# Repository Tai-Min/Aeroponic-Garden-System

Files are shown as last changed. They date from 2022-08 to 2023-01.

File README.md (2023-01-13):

# Thingy:53 Aeroponic Garden
2nd place in [Smarter Sustainable World Challenge
with Nordic Semiconductor](https://www.hackster.io/contests/smarter-sustainable-world). For details of the project itself see [Vertical Self Regulating Soilless Farm](https://www.hackster.io/Tai-Min/vertical-self-regulating-soilless-farm-a86d25)

## Physical setup
### The pot
* Print heater_bottom_n.stl and heater_top_n.stl (n = 1, 2, 3, 4) and glue them together. Insert 12V 5050 fan into place
* Print funnel.stl and insert it into heater glued in previous step
* Print num_layers * 4 layer_quarter.stl and glue them together then stack the layers and place them on top of the heater
* Print num_layers nozzle_frame.stl and num_layers * 4 nozzle_single.stl and glue them together then using straight plastic pipe assemble them starting from funnel's center intlet so that each nozzle_frame is on the level of the pot of given layer  
* Print nozzle_frame_end.stl and insert it at the top of previously created piping
* Print top_hat.stl and insert it at the top of vertical pot then insert Thingy:53 into it 
* Create wooden frame as in the pictures below
* Print valve_holder.stl and screw it at the bottom of the wooden quadropod then screw 12V valves into places
* Print num_layers * 4 - 1 of water_nozzle_frame.stl and nozzle_single.stl and glue them together then screw them on wooden structure so that each nozzle faces one pot
* Print 1 water_nozzle_frame_end.stl and single_nozzle.stl and glue them together and screw it on the wooden structure so it faces one pot
* Install LED strips on wooden structure so each pot has it's own light source

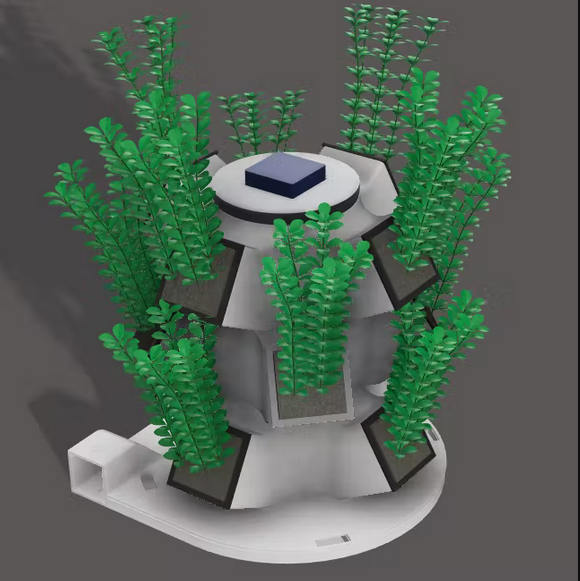
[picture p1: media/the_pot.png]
Pot assembly 1

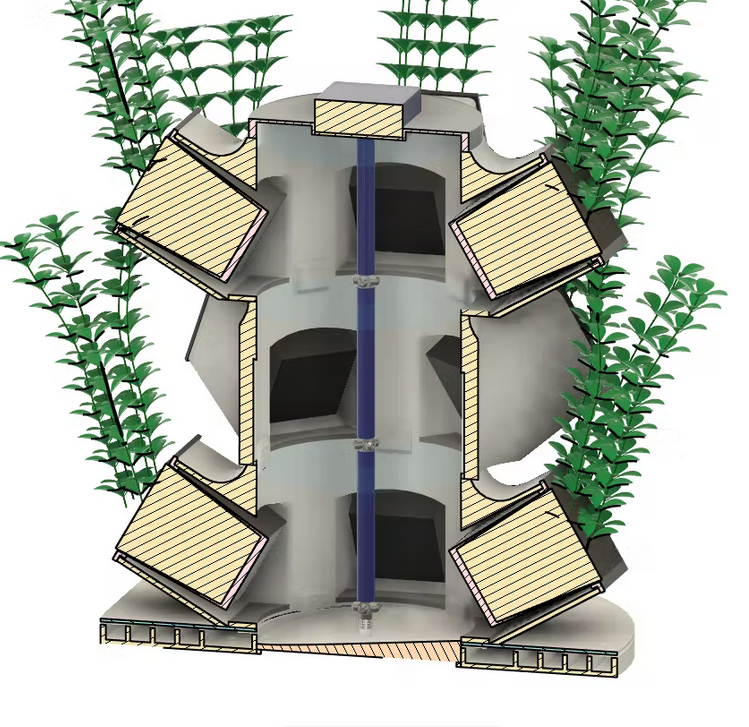
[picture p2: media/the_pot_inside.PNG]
Pot assembly 2

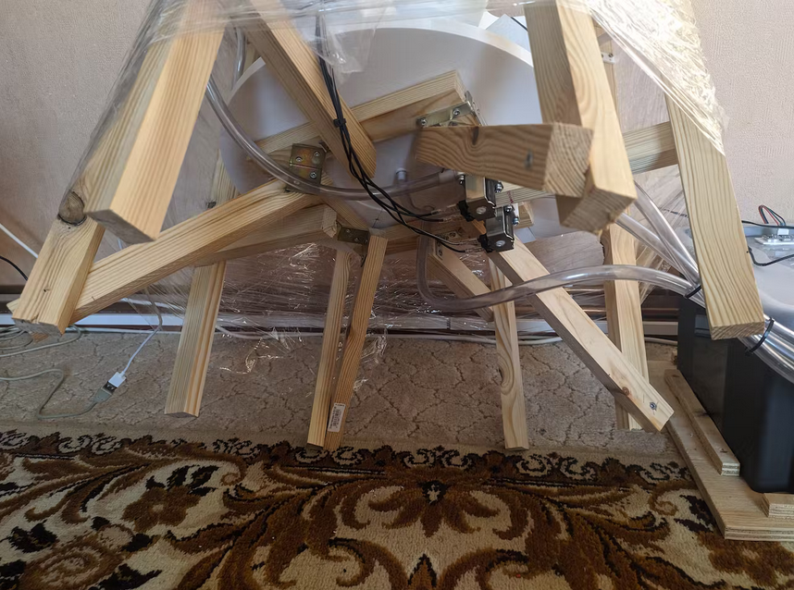
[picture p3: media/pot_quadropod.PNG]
Pot assembly bottom

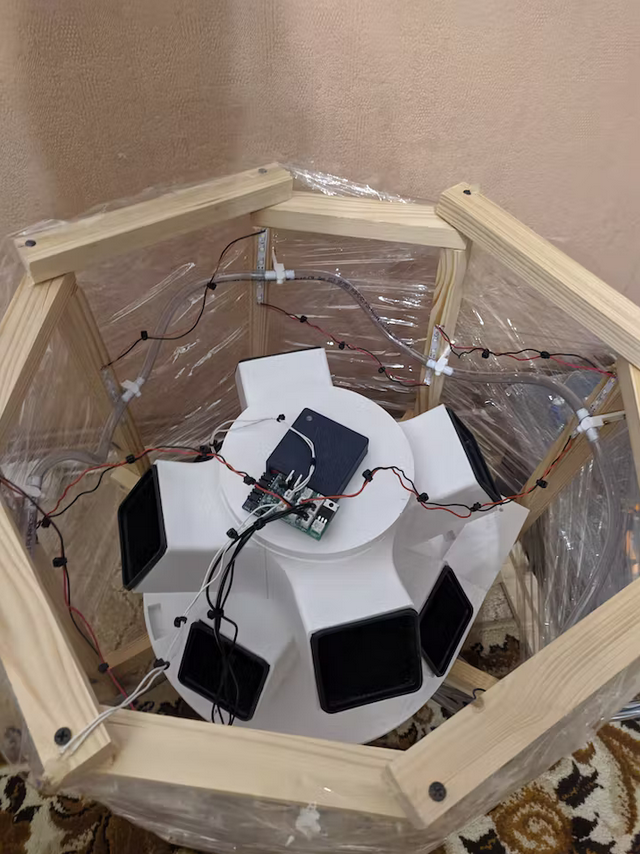
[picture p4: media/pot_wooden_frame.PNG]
Pot assembly frame


### RPi water system
* Print 2 pipe_holder_1.stl and pipe_holder_2.stl and glue them together on the side of both liquid tanks
* Print 2 pump_holder.stl and glue it at the bottom of the tank then screw the 12V pump into it
* Print 2 water_level_holder.stl, place it on the lids of both liquid tanks and then snap an ultrasonic sensor into them
* Screw reed switches into both liquid tanks and corresponding magnets into lids
* On nutrition water tank mount PCBs for EC and pH sensors and place the sensors into the tank itself
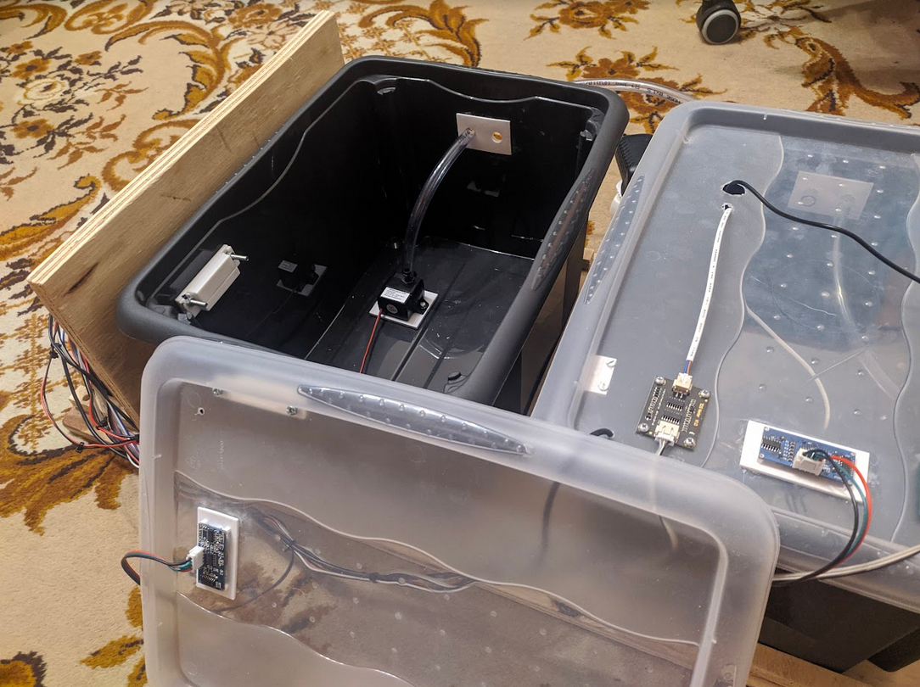
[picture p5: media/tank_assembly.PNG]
Tank assembly


### Putting it together
Use flexible piping to connect the pot to water system as in the block diagram below:
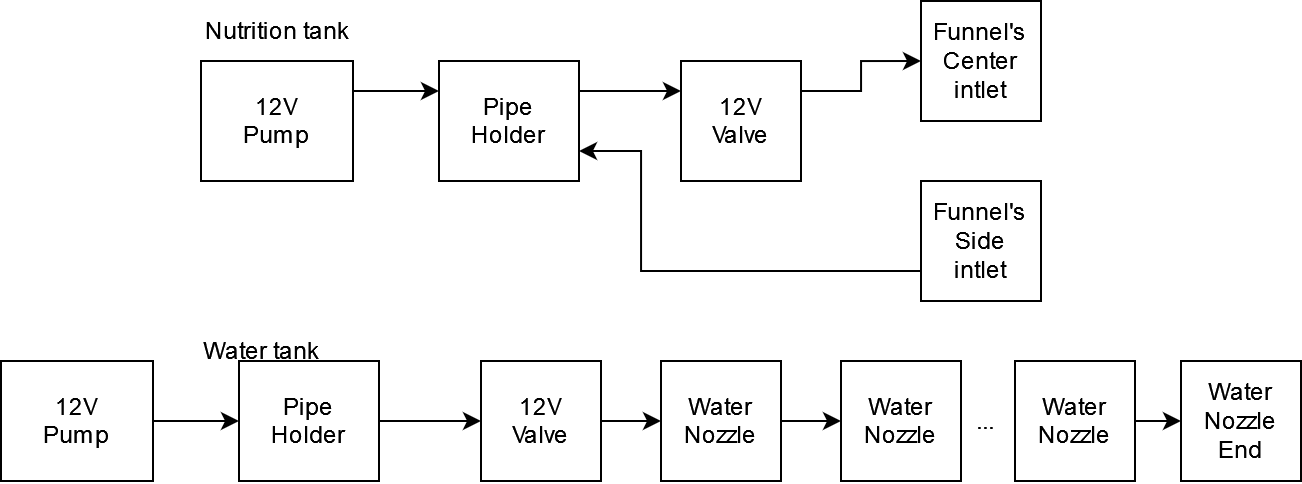
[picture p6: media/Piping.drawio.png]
Piping diagram


## Electronics
Refer to KiCad project in /pi_shield folder for BOM and assembly purposes of the hats.

### The pot
Connect sensors / actuators to Thingy:53 control hat as in the block diagram below:
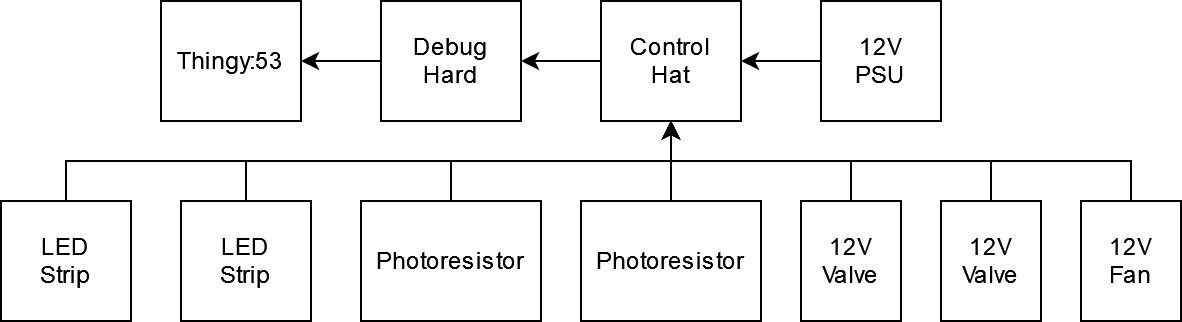
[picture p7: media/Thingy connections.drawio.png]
Thingy:53 connections


### RPi water system
Connect sensors / actuators to RPi's control hat as in the block diagram below:
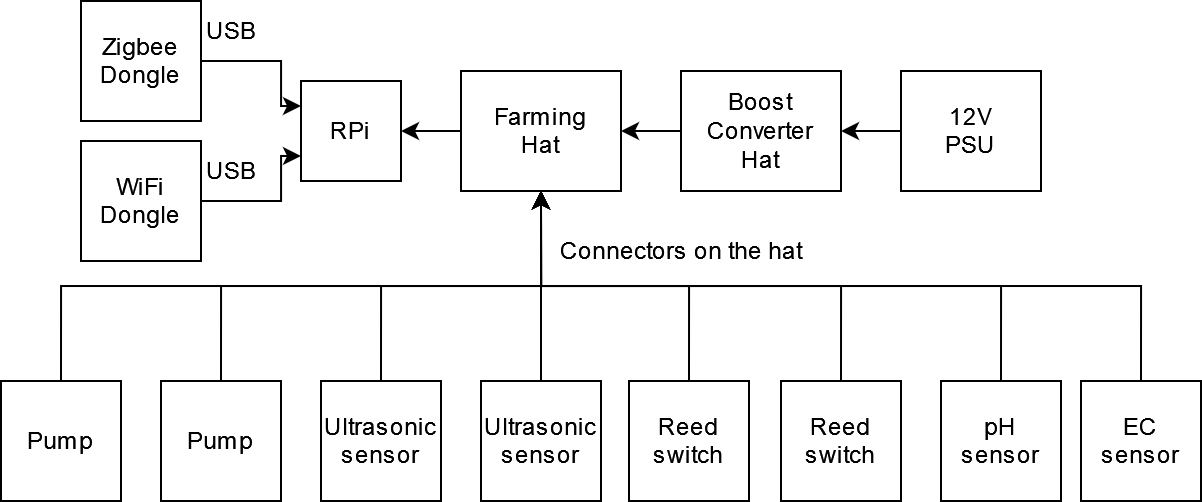
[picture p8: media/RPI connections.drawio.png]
RPi connections

## Attiny85
* Connect some programmer (i.e. ArduinoISP or USBasp) to Attiny85
* In platformio.ini change upload_protocol to your programmer
* You might also want to fine tune PH_MAGIC_NUMBER, TDS_A, TDS_B variables to match your sensor's characteristics
* In PlatformIO menu press "Set Fuses" in "attiny85" configuration, then click "Upload"
* Insert Attiny85 into Farm Overseers's shield

## Farm Overseer setup
* Setup Ubuntu Server 20.04 (i.e via [Raspberry Pi Imager](https://www.raspberrypi.com/software/))

### Enable UART
* Disable serial console
```
sudo systemctl stop serial-getty@ttyS0.service
sudo systemctl disable serial-getty@ttyS0.service
sudo systemctl mask serial-getty@ttyS0.service
```
* Put below into /etc/udev/rules.d/10-local.rules
```
KERNEL=="ttyS0", SYMLINK+="serial0" GROUP="tty" MODE="0660"
KERNEL=="ttyAMA0", SYMLINK+="serial1" GROUP="tty" MODE="0660"
```
* Reload udev rules
```
sudo udevadm control --reload-rules && sudo udevadm trigger
```
* Add user to tty (edit parts in "<>")
```
sudo adduser <USER> tty
```
* Delete below from /boot/firmware/cmdline.txt
```
console=serial0,115200
```
* Add below to /boot/firmware/config.txt
```
dtoverlay=disable-bt
```
### Enable 1-Wire
* Add below to /boot/firmware/config.txt
```
dtoverlay=w1-gpio,gpiopin=4
```

### ROS2
* Install [ROS2 Foxy Base version](https://docs.ros.org/en/foxy/Installation/Ubuntu-Install-Debians.html)
* Clone this repo to your home directory (/home/$USER/TODO)
* Build ROS components:
```bash
cd ~/TODO/ros_workspace && colcon build
```
* Place ROS setups in your .bashrc (edit parts in "<>")
```
source /opt/ros/foxy/setup.bash
source /home/<USER>/TODO/ros_workspace/install/setup.bash

```
### Mosquitto
* Install mosquitto 2.0
```
sudo add-apt-repository -y ppa:mosquitto-dev/mosquitto-ppa
sudo apt install mosquitto
sudo systemctl enable mosquitto
```

### zigbee2mqtt
* Install [zigbee2mqtt](https://www.zigbee2mqtt.io/guide/installation/01_linux.html) and set it to start as a daemon on boot. Use following config (edit parts in "<>"):
```yaml
mqtt:
  base_topic: field
  server: 'mqtt://localhost'

serial:
  port: <YOUR ZIGBEE DONGLE PORT>

advanced:
    network_key: GENERATE

external_converters:
  - fc.js
```

Create file /opt/zigbee2mqtt/data/fc.js and paste following into it:
```js
const fz = require('zigbee-herdsman-converters/converters/fromZigbee');
const tz = require('zigbee-herdsman-converters/converters/toZigbee');
const exposes = require('zigbee-herdsman-converters/lib/exposes');
const reporting = require('zigbee-herdsman-converters/lib/reporting');

const definition = {
    zigbeeModel: ['FC_v0.1'],
    model: 'FC',
    vendor: 'Nordic',
    description: 'Field Controller',
    fromZigbee: [fz.temperature, fz.humidity, fz.pressure, fz.on_off, fz.level_config],
    toZigbee: [tz.on_off, tz.level_config],
    exposes: [],
    configure: async (device, coordinatorEndpoint, logger) => {
        await reporting.bind(device.getEndpoint(16), coordinatorEndpoint, ['msTemperatureMeasurement']);
        await reporting.temperature(device.getEndpoint(16), { min: 30, max: 30, change: 0 });

        await reporting.bind(device.getEndpoint(16), coordinatorEndpoint, ['msPressureMeasurement']);
        await reporting.pressure(device.getEndpoint(16), { min: 30, max: 30, change: 0 });

        await reporting.bind(device.getEndpoint(16), coordinatorEndpoint, ['msRelativeHumidity']);
        await reporting.humidity(device.getEndpoint(16), { min: 30, max: 30, change: 0 });
    },
    endpoint: (device) => {
        return { fan: 10, led1: 11, led2: 12, strat: 13, water_valve: 14, nutri_valve: 15, sensors: 16 };
    },
};

module.exports = definition;
```

### Finishing up
* Reboot the board
```
sudo reboot now
```

## Field controller setup
Open field_controller/ in VSCode with nRF Connect and with Thingy:53 connected via JLink press flash.

## Run Farm Overseer's control algorithms
SSH into the Farm Overseer and run:
```
ros2 launch garden_meta system.launch.py
```

## Pair field controller to Farm Overseer
With Field Controller running cd into scripts/ and run:
```
./pair.sh -t 300
``` 
This will enable pairing for 300 seconds and should pair with the Field Controller.

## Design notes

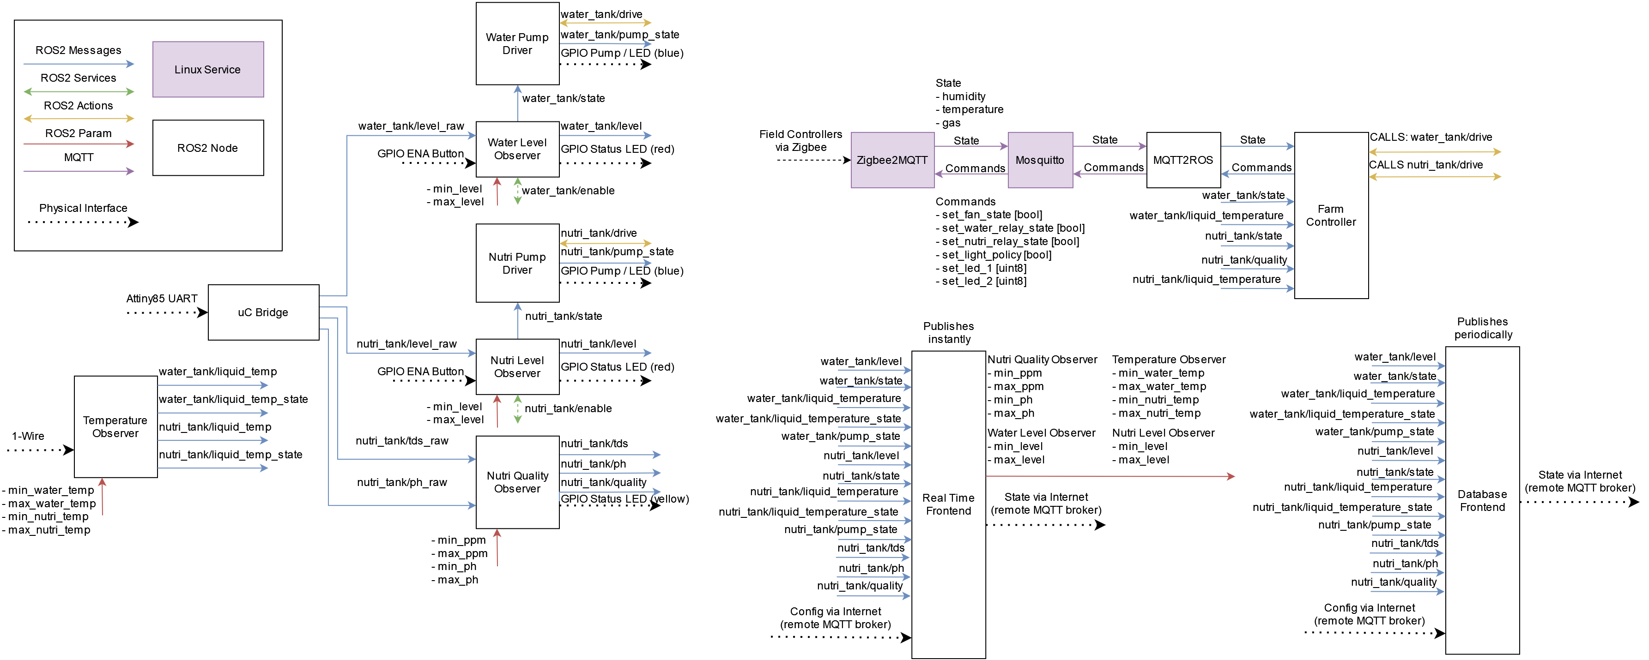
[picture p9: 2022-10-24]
media/controller_software.drawio.png

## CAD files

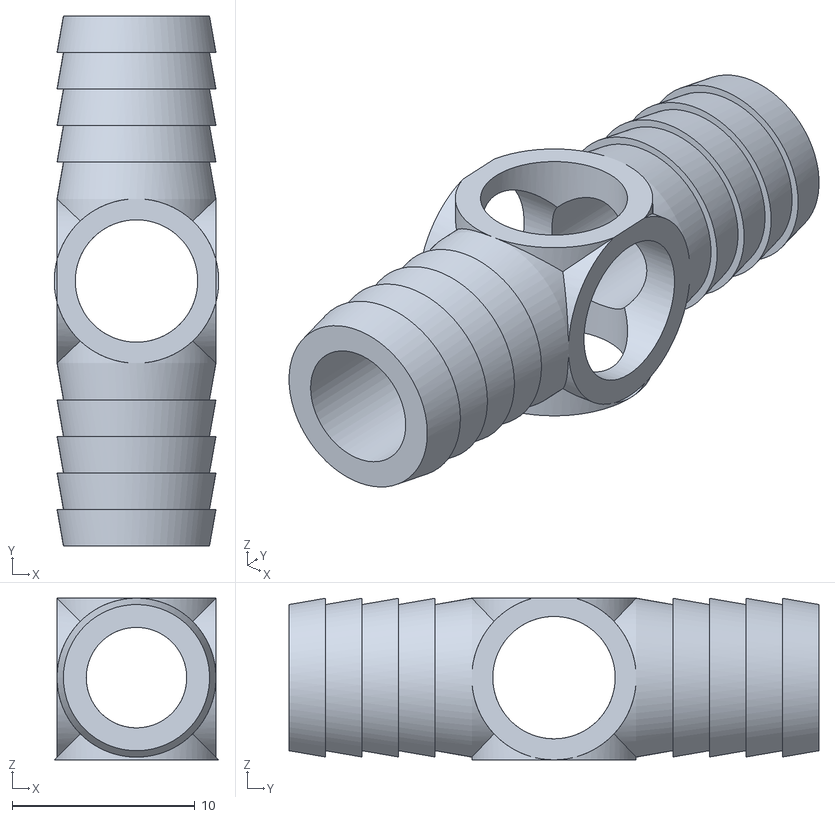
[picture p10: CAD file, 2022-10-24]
stl/nozzle_frame.stl
9.00 x 29.0 x 8.85

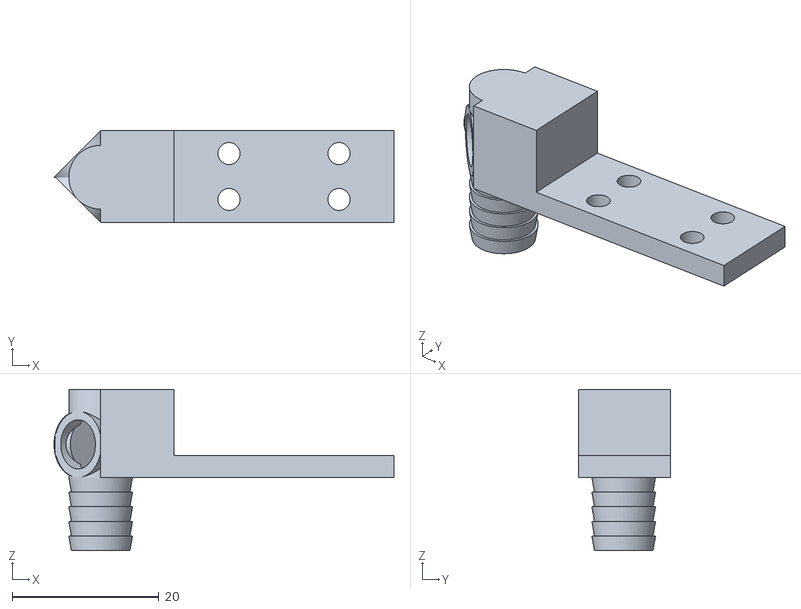
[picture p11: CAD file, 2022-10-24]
stl/water_nozzle_frame_end.stl
46.4 x 12.5 x 22.0

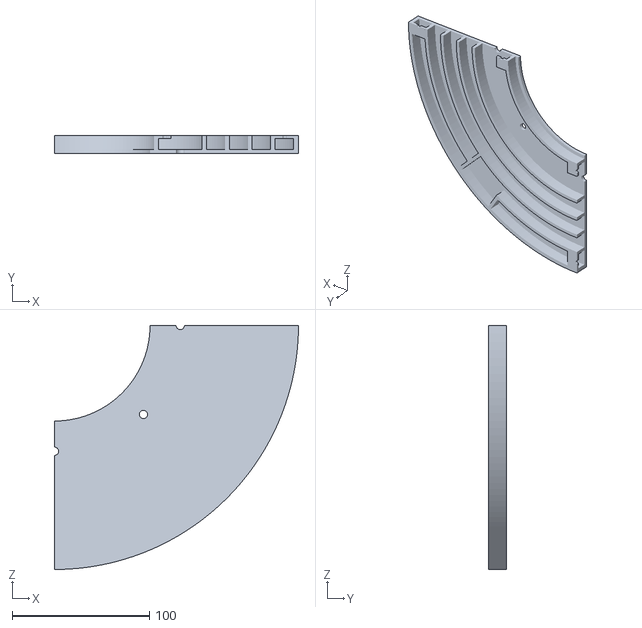
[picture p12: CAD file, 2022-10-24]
stl/heater_bottom_2.stl
177.5 x 13.0 x 177.5

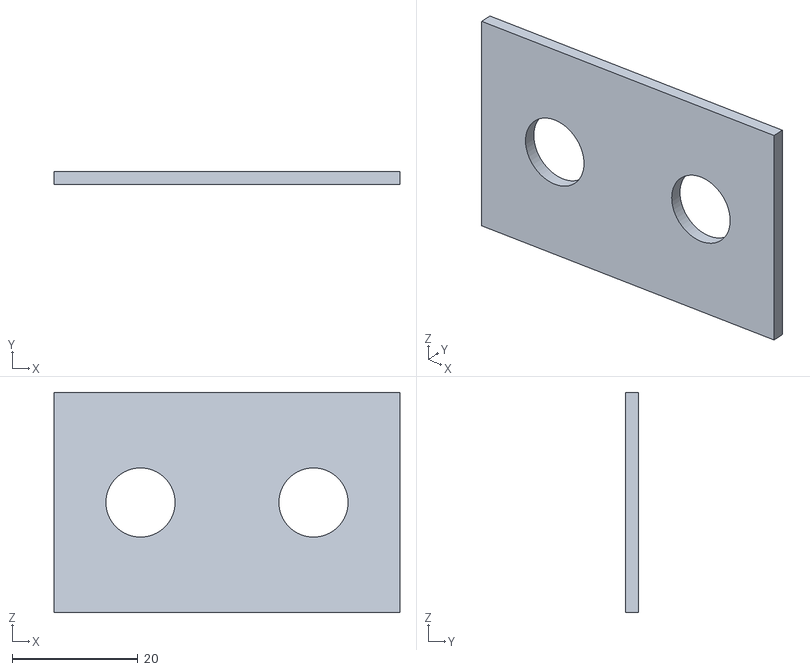
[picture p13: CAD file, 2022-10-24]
stl/pipe_holder_1.stl
55.0 x 2.00 x 35.0

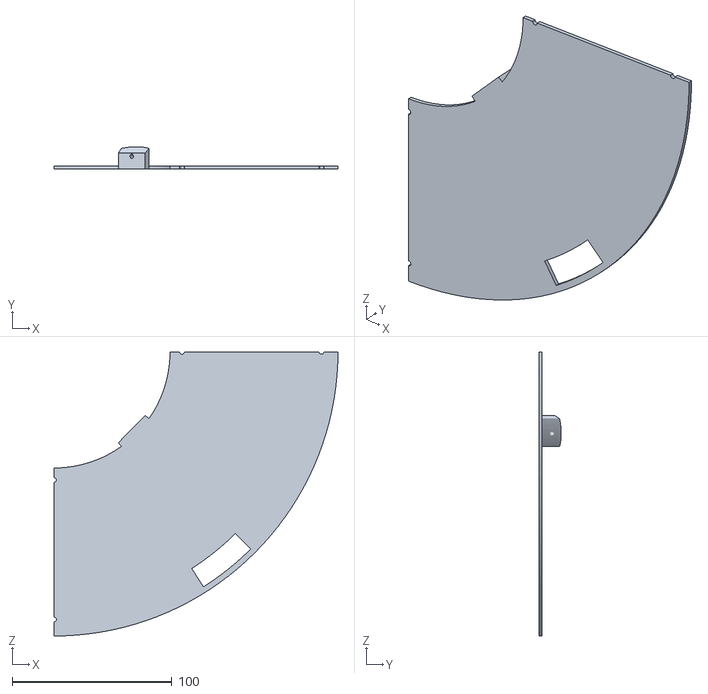
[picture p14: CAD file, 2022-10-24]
stl/heater_top_3.stl
177.5 x 14.0 x 177.5

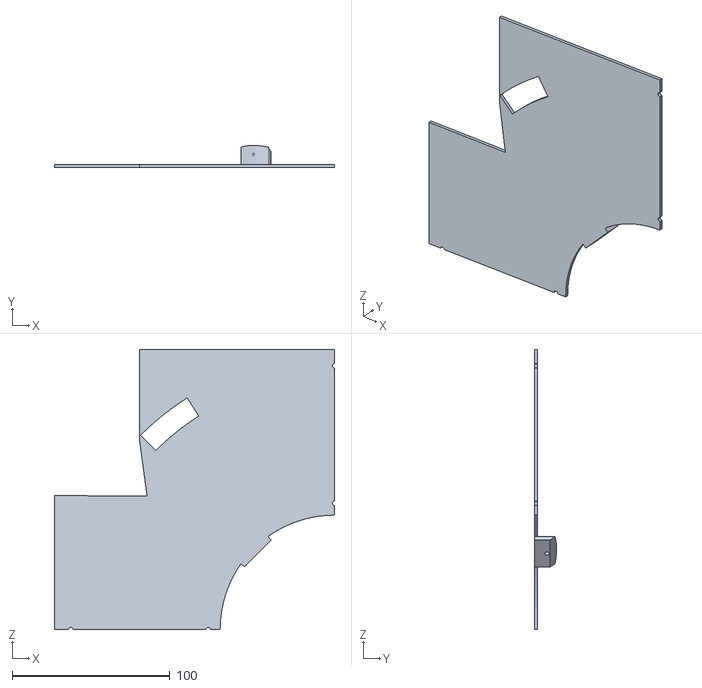
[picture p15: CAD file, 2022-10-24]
stl/heater_top_1.stl
177.4 x 14.0 x 177.5

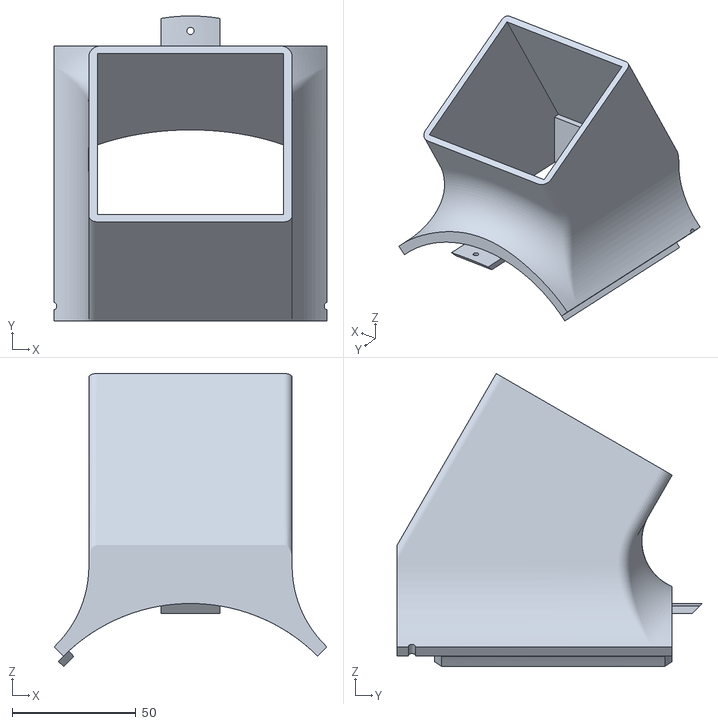
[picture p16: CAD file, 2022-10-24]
stl/layer quarter.stl
110.0 x 123.0 x 118.2

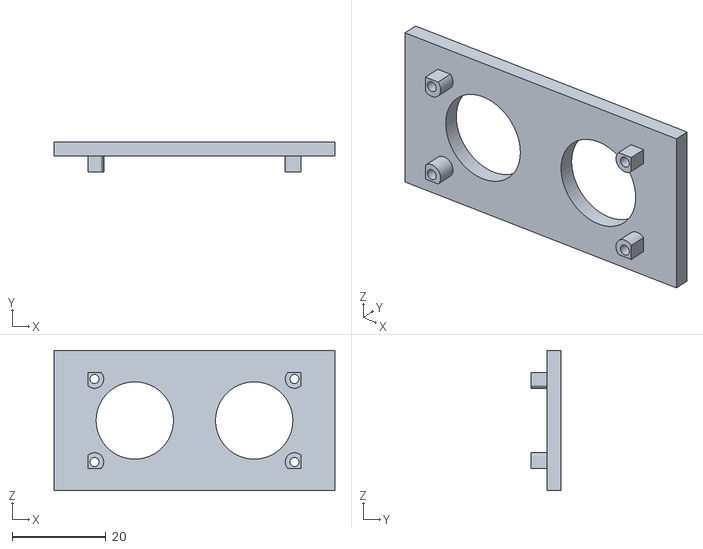
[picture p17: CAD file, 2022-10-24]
stl/water_level_holder.stl
60.0 x 6.50 x 30.0

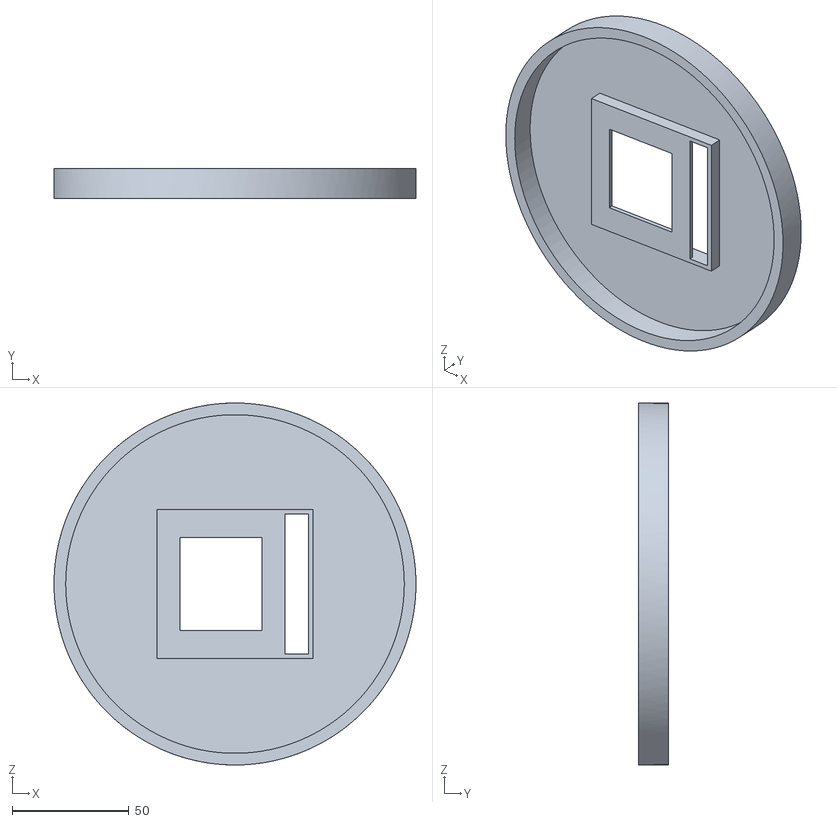
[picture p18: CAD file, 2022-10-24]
stl/top_hat.stl
155.0 x 13.0 x 155.0

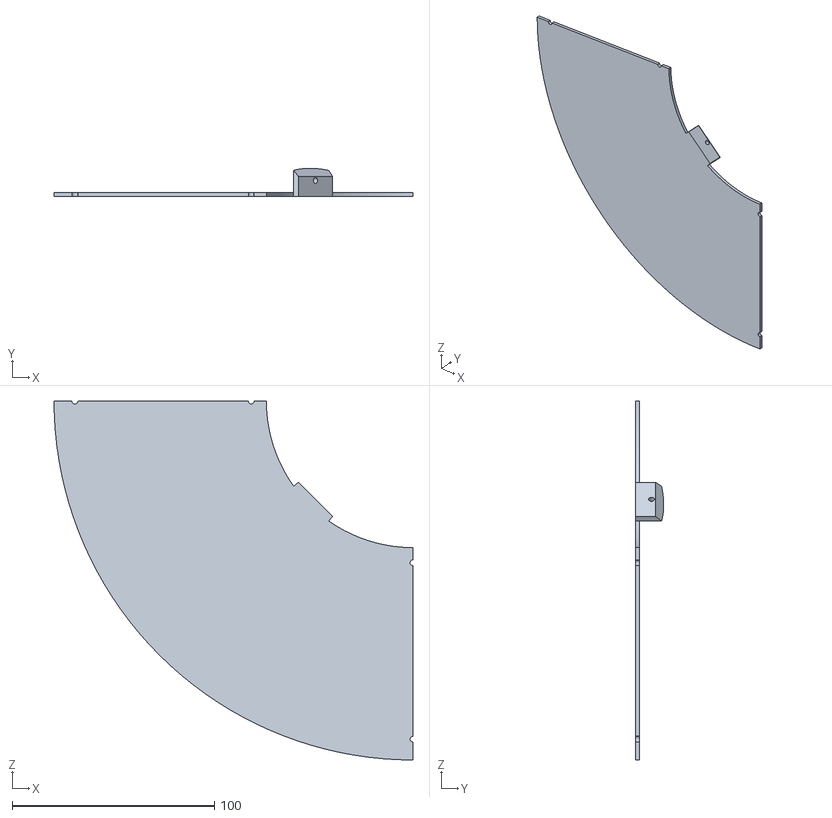
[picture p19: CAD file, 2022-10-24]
stl/heater_top_2.stl
177.5 x 14.0 x 177.5

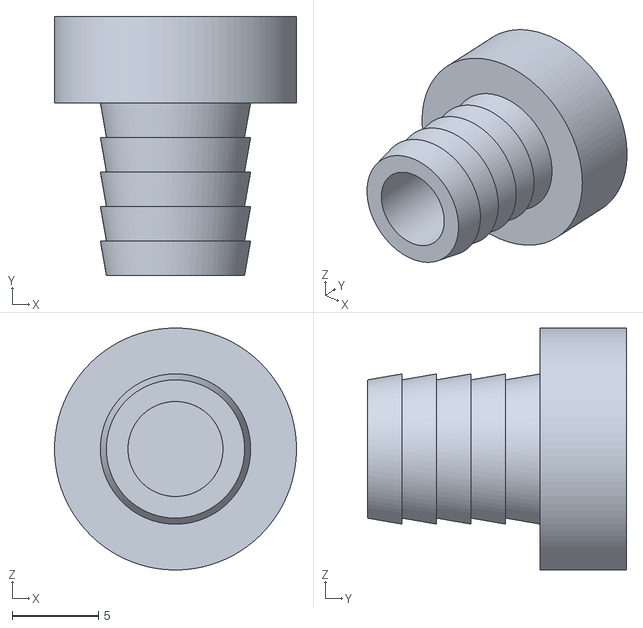
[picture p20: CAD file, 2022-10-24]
stl/nozzle_frame_end.stl
14.0 x 15.0 x 14.0

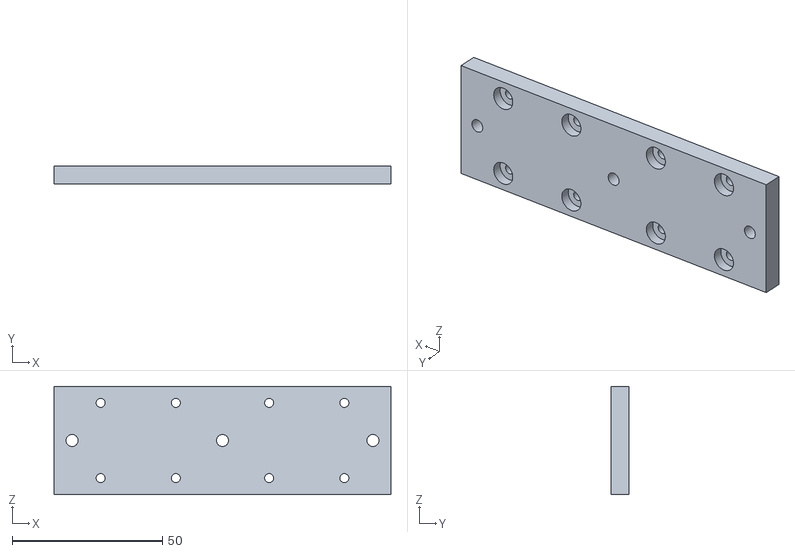
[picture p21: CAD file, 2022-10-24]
stl/valve_holder.stl
112.0 x 6.00 x 36.0

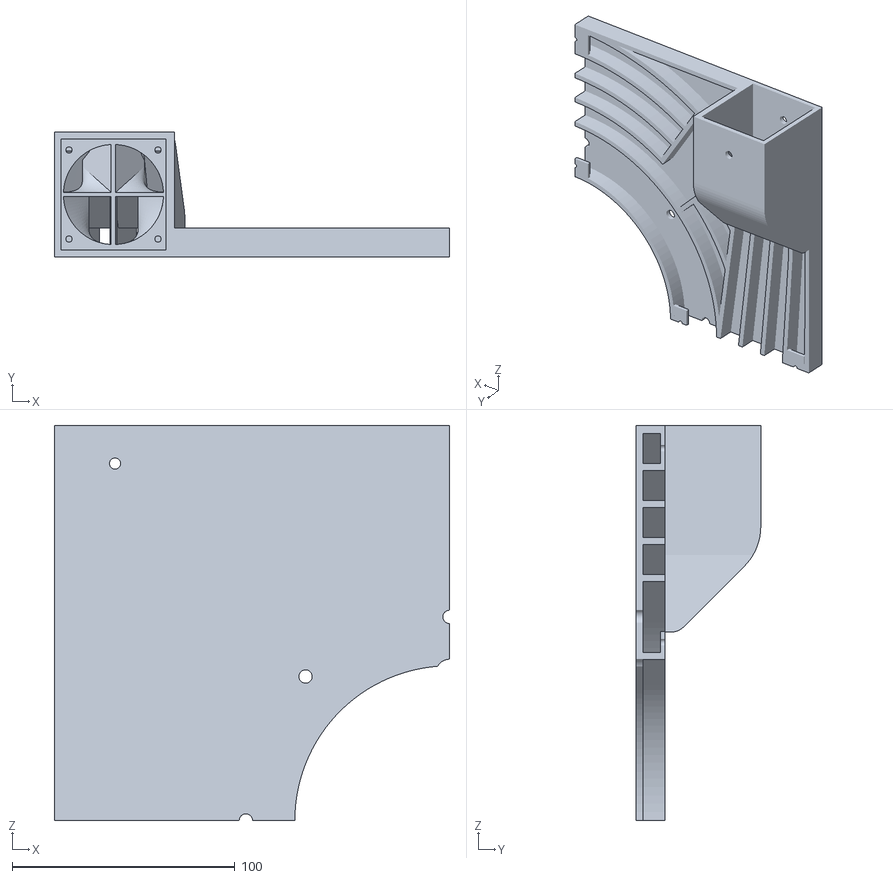
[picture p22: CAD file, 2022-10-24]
stl/heater_bottom_4.stl
177.5 x 56.0 x 177.5

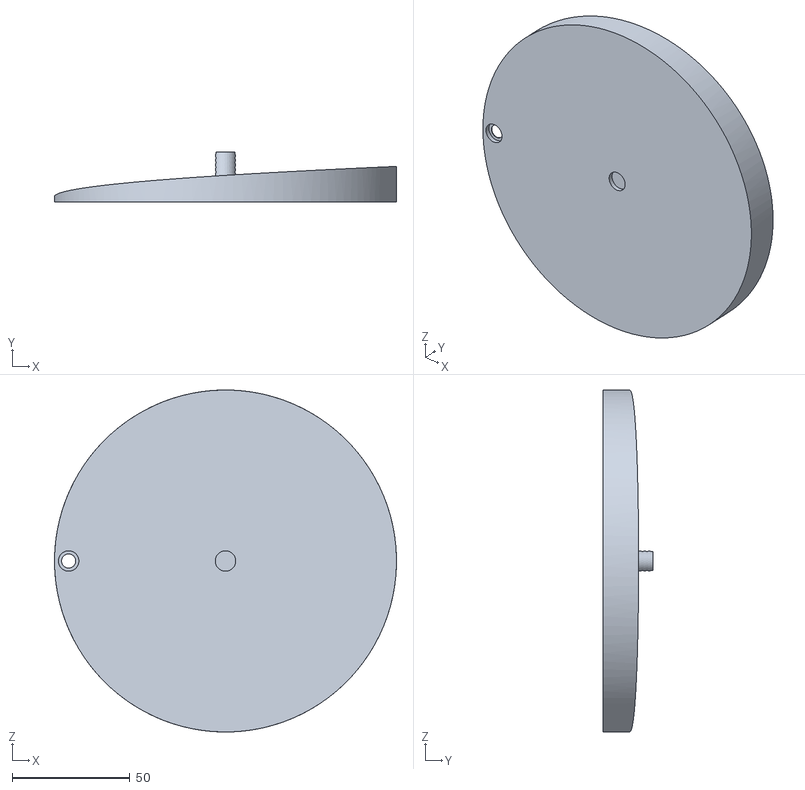
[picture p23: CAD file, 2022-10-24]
stl/funnel.stl
145.0 x 21.0 x 145.0

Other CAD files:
stl/heater_top_4.stl
stl/heater_bottom_1.stl
stl/nozzle_single.stl
stl/pipe_holder_2.stl
stl/heater_bottom_3.stl
stl/pump_holder.stl
stl/water_nozzle_frame.stl

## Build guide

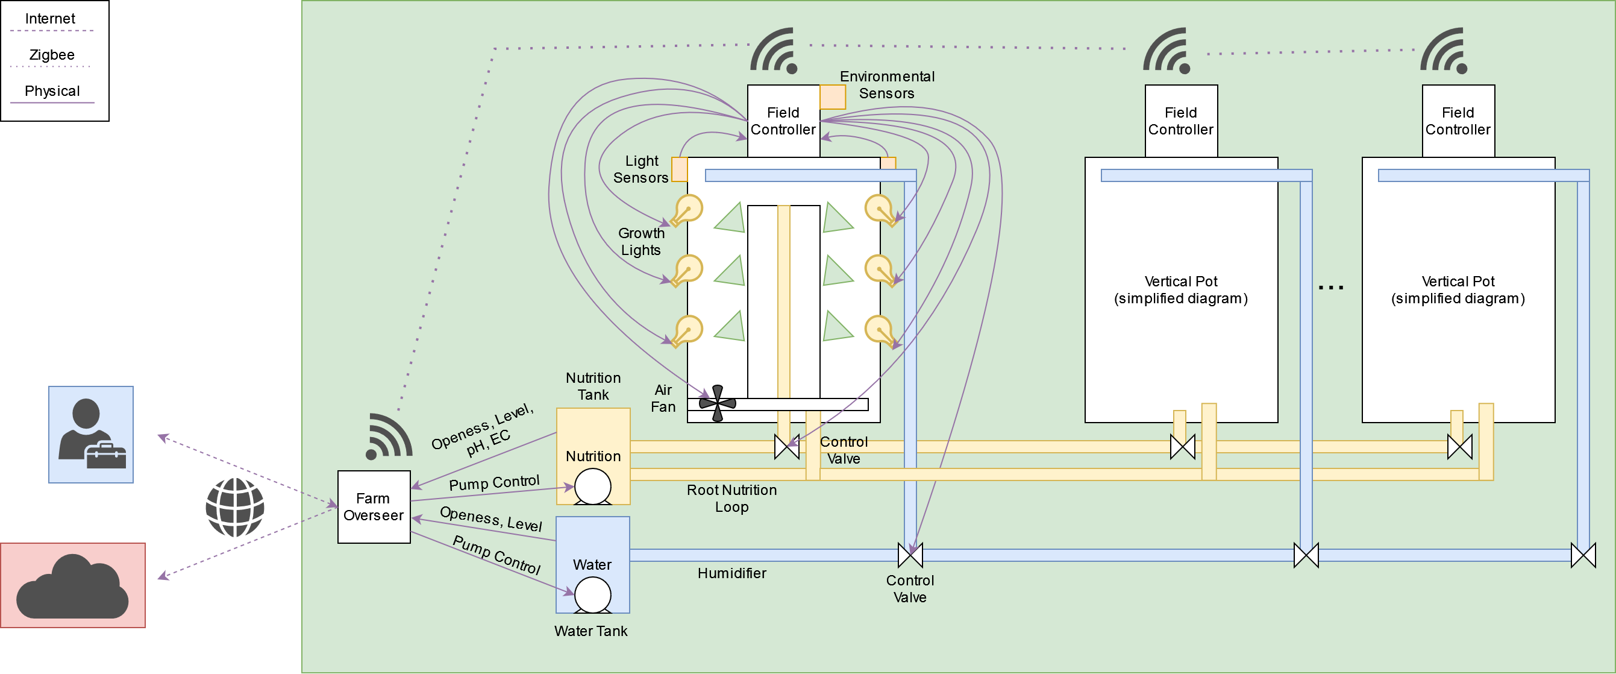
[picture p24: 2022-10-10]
media/system_setup_detailed.drawio.png

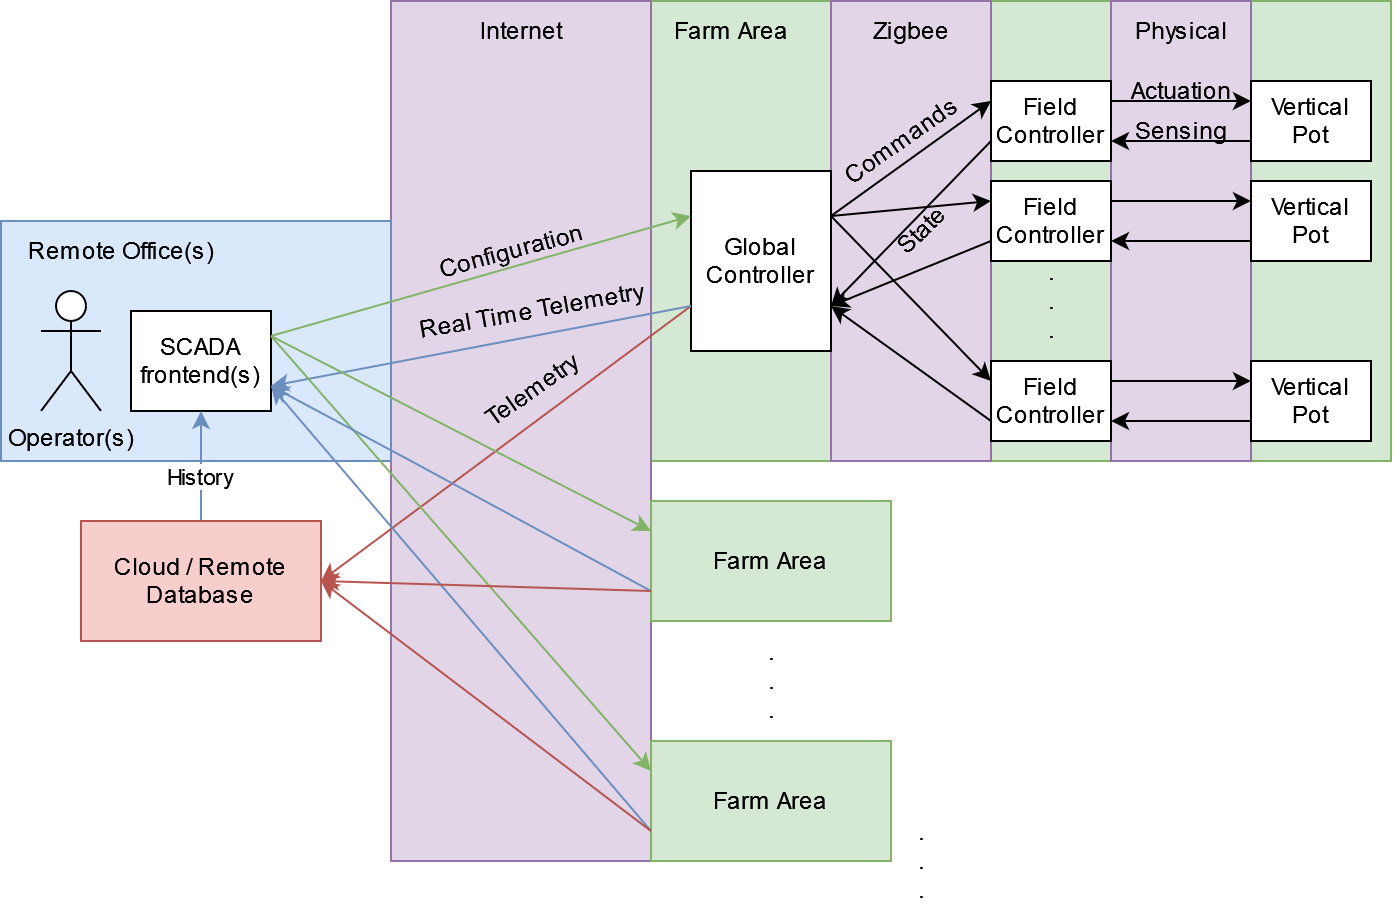
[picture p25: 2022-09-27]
media/system_setup.drawio.png

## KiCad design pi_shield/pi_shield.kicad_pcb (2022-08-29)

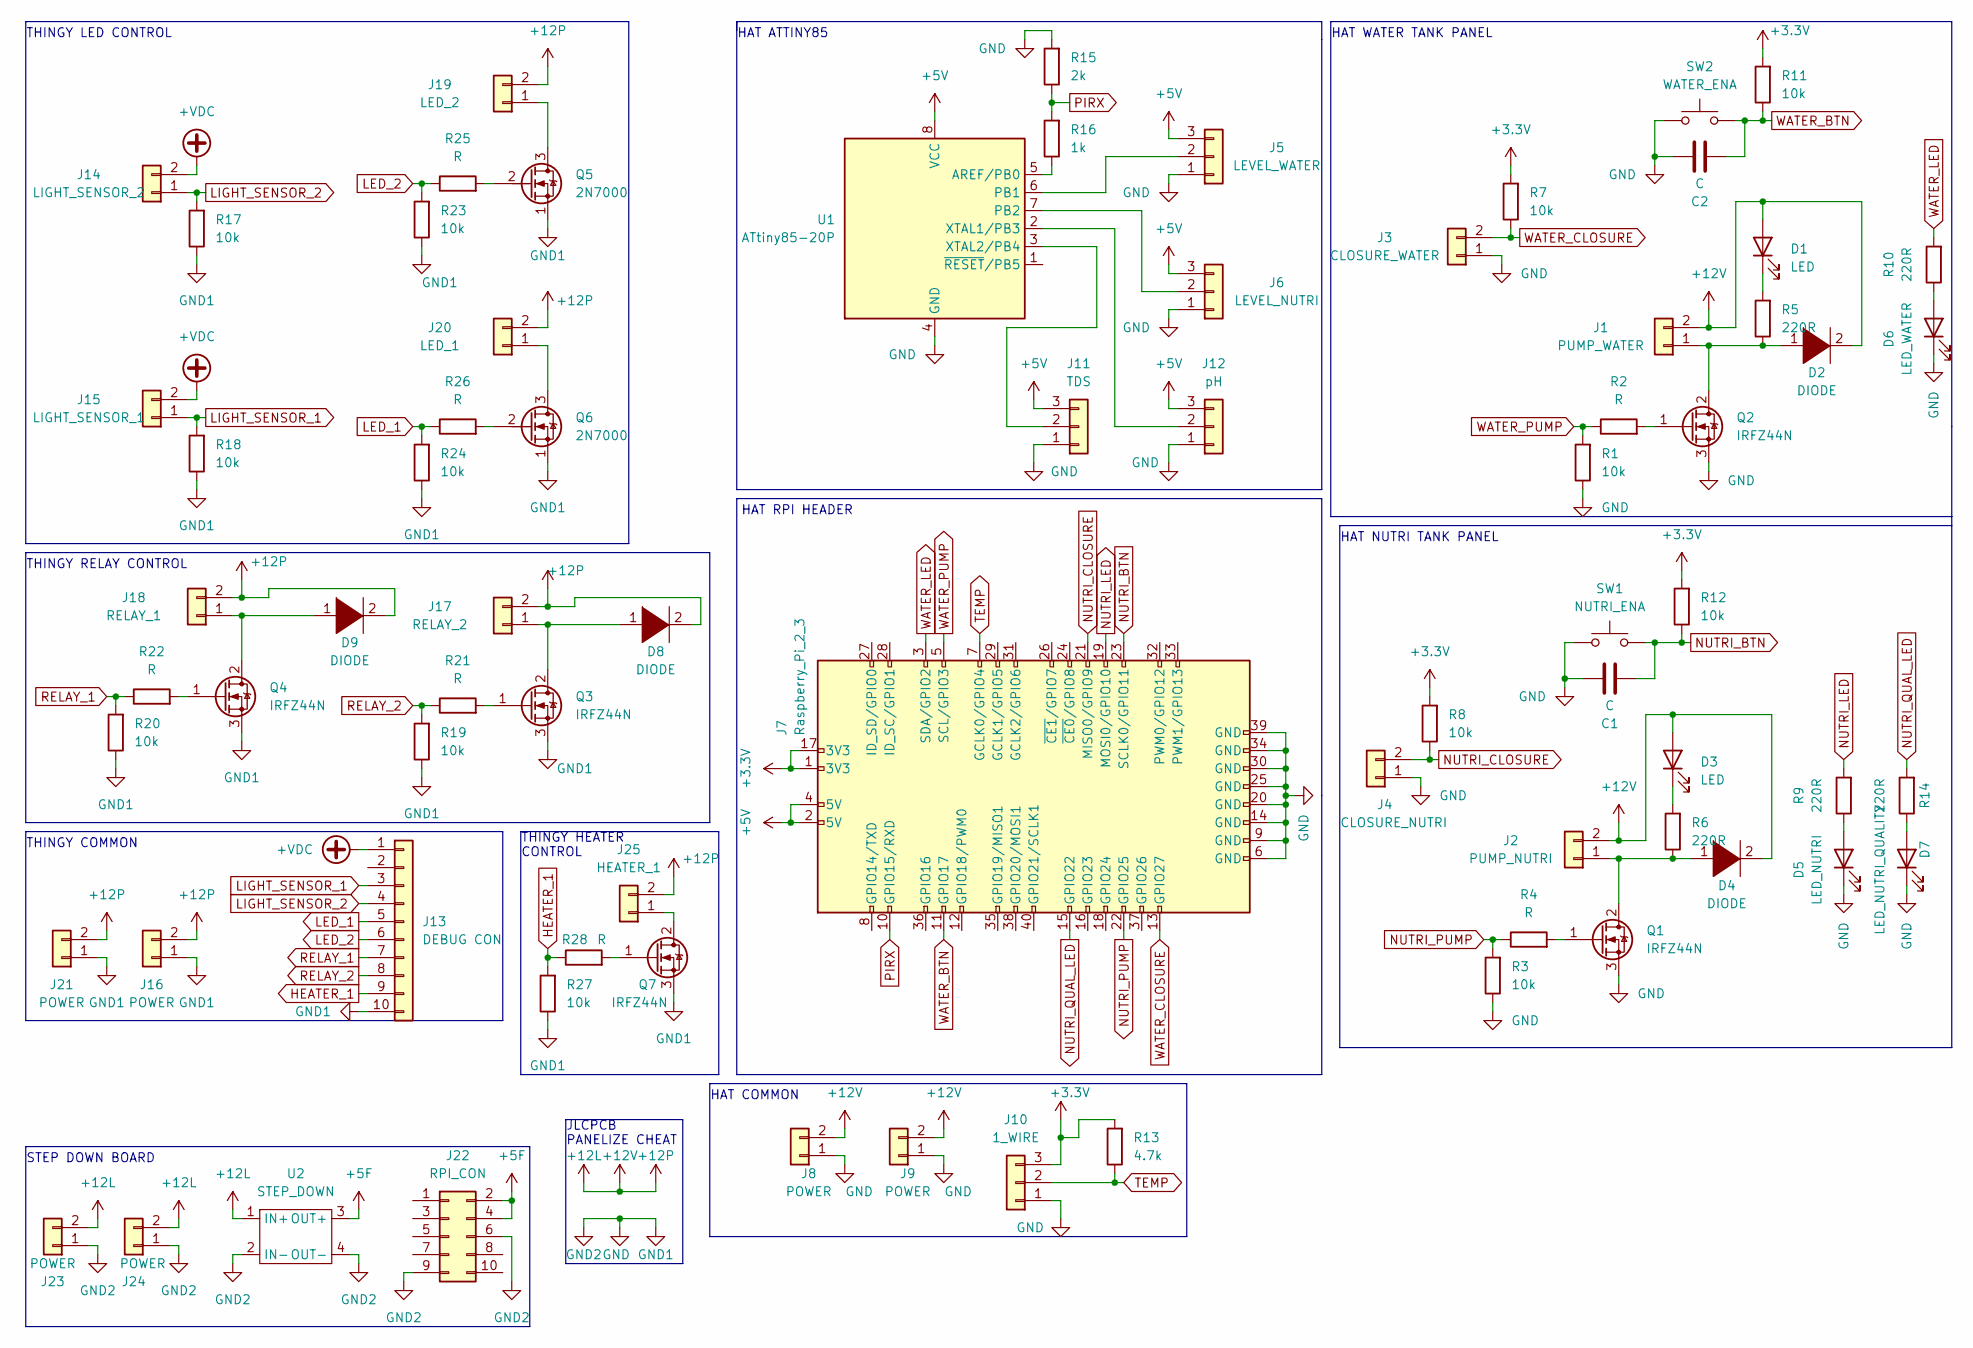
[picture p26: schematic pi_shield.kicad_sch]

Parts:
C1, C2: C; C_Disc_D5.0mm_W2.5mm_P2.50mm
D1, D3: LED; LED_D5.0mm_Clear
D2: DIODE; D_DO-15_P2.54mm_Vertical_AnodeUp
D4, D8, D9: DIODE; D_A-405_P2.54mm_Vertical_AnodeUp
D5: LED_NUTRI; LED_D5.0mm_Clear
D6: LED_WATER; LED_D5.0mm_Clear
D7: LED_NUTRI_QUALITY; LED_D5.0mm_Clear
J1: PUMP_WATER; Molex_SL_171971-0002_1x02_P2.54mm_Vertical
J2: PUMP_NUTRI; Molex_SL_171971-0002_1x02_P2.54mm_Vertical
J3: CLOSURE_WATER; Molex_SL_171971-0002_1x02_P2.54mm_Vertical
J4: CLOSURE_NUTRI; Molex_SL_171971-0002_1x02_P2.54mm_Vertical
J5: LEVEL_WATER; Molex_SL_171971-0003_1x03_P2.54mm_Vertical
J6: LEVEL_NUTRI; Molex_SL_171971-0003_1x03_P2.54mm_Vertical
J7: Raspberry_Pi_2_3; raspberrypi_2_3
J8, J9, J16, J21, J23, J24: POWER; Molex_SL_171971-0002_1x02_P2.54mm_Vertical
J10: 1_WIRE; Molex_SL_171971-0003_1x03_P2.54mm_Vertical
J11: TDS; Molex_SL_171971-0003_1x03_P2.54mm_Vertical
J12: pH; Molex_SL_171971-0003_1x03_P2.54mm_Vertical
J13: DEBUG CON; PinSocket_1x10_P2.54mm_Vertical
J14: LIGHT_SENSOR_2; Molex_SL_171971-0002_1x02_P2.54mm_Vertical
J15: LIGHT_SENSOR_1; Molex_SL_171971-0002_1x02_P2.54mm_Vertical
J17: RELAY_2; Molex_SL_171971-0002_1x02_P2.54mm_Vertical
J18: RELAY_1; Molex_SL_171971-0002_1x02_P2.54mm_Vertical
J19: LED_2; Molex_SL_171971-0002_1x02_P2.54mm_Vertical
J20: LED_1; Molex_SL_171971-0002_1x02_P2.54mm_Vertical
J22: RPI_CON; PinSocket_2x05_P2.54mm_Vertical
J25: HEATER_1; Molex_SL_171971-0002_1x02_P2.54mm_Vertical
Q1, Q2, Q7: IRFZ44N; TO-220-3_Horizontal_TabDown
Q3, Q4: IRFZ44N; TO-220-3_Vertical
Q5, Q6: 2N7000; TO-92L_Inline
R1, R3, R7, R8, R11, R12, R17, R18, R19, R20, R23, R24, R27: 10k; R_Axial_DIN0204_L3.6mm_D1.6mm_P2.54mm_Vertical
R2, R4, R21, R22, R25, R26, R28: R; R_Axial_DIN0204_L3.6mm_D1.6mm_P2.54mm_Vertical
R5, R6, R9, R10, R14: 220R; R_Axial_DIN0204_L3.6mm_D1.6mm_P2.54mm_Vertical
R13: 4.7k; R_Axial_DIN0204_L3.6mm_D1.6mm_P2.54mm_Vertical
R15: 2k; R_Axial_DIN0204_L3.6mm_D1.6mm_P2.54mm_Vertical
R16: 1k; R_Axial_DIN0204_L3.6mm_D1.6mm_P2.54mm_Vertical
SW1: NUTRI_ENA; SW_PUSH_6mm
SW2: WATER_ENA; SW_PUSH_6mm
U1: ATtiny85-20P; DIP-8_W7.62mm
U2: STEP_DOWN; SRT_MPT1584EN_Module

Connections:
+3.3V: J7.1 (3V3), J7.17 (3V3), J10.3, R7.2, R8.2, R11.2, R12.2, R13.2
+5F: J22.2, J22.4, U2.3 (OUT+)
+5V: J5.3, J6.3, J7.2 (5V), J7.4 (5V), J11.3, J12.3, U1.8 (VCC)
+12L: D1.2 (A), D2.2 (A), D3.2 (A), D4.2 (A), D8.2 (A), D9.2 (A), J1.2, J2.2, J8.2, J9.2, J16.2, J17.2, J18.2, J19.2, J20.2, J21.2, J23.2, J24.2, J25.2, U2.1 (IN+)
+VDC: J13.1, J14.2, J15.2
GND: C1.1, C2.1, D5.1 (K), D6.1 (K), D7.1 (K), J3.1, J4.1, J5.1, J6.1, J7.6 (GND), J7.9 (GND), J7.14 (GND), J7.20 (GND), J7.25 (GND), J7.30 (GND), J7.34 (GND), J7.39 (GND), J8.1, J9.1, J10.1, J11.1, J12.1, J13.10, J16.1, J21.1, J22.6, J22.9, J23.1, J24.1, Q1.3 (S), Q2.3 (S), Q3.3 (S), Q4.3 (S), Q5.1 (S), Q6.1 (S), Q7.3 (S), R1.1, R3.1, R15.2, R17.1, R18.1, R19.1, R20.1, R23.1, R24.1, R27.1, SW1.1, SW2.1, U1.4 (GND), U2.2 (IN-), U2.4 (OUT-)
HEATER_1: J13.9, R27.2, R28.1
LED_1: J13.5, R24.2, R26.1
LED_2: J13.6, R23.2, R25.1
LIGHT_SENSOR_1: J13.3, J15.1, R18.2
LIGHT_SENSOR_2: J13.4, J14.1, R17.2
NUTRI_BTN: C1.2, J7.23 (SCLK0/GPIO11), R12.1, SW1.2
NUTRI_CLOSURE: J4.2, J7.21 (MISO0/GPIO9), R8.1
NUTRI_LED: J7.19 (MOSI0/GPIO10), R9.2
NUTRI_PUMP: J7.22 (GPIO25), R3.2, R4.1
NUTRI_QUAL_LED: J7.15 (GPIO22), R14.2
unnamed: D1.1 (K), R5.2
unnamed: D2.1 (K), J1.1, Q2.2 (D), R5.1
unnamed: D3.1 (K), R6.2
unnamed: D4.1 (K), J2.1, Q1.2 (D), R6.1
unnamed: D5.2 (A), R9.1
unnamed: D6.2 (A), R10.1
unnamed: D7.2 (A), R14.1
unnamed: D8.1 (K), J17.1, Q3.2 (D)
unnamed: D9.1 (K), J18.1, Q4.2 (D)
unnamed: J5.2, U1.6 (PB1)
unnamed: J6.2, U1.7 (PB2)
unnamed: J11.2, U1.3 (XTAL2/PB4)
unnamed: J12.2, U1.2 (XTAL1/PB3)
unnamed: J19.1, Q5.3 (D)
unnamed: J20.1, Q6.3 (D)
unnamed: J25.1, Q7.2 (D)
unnamed: Q1.1 (G), R4.2
unnamed: Q2.1 (G), R2.2
unnamed: Q3.1 (G), R21.2
unnamed: Q4.1 (G), R22.2
unnamed: Q5.2 (G), R25.2
unnamed: Q6.2 (G), R26.2
unnamed: Q7.1 (G), R28.2
unnamed: R16.1, U1.5 (AREF/PB0)
PIRX: J7.10 (GPIO15/RXD), R15.1, R16.2
RELAY_1: J13.7, R20.2, R22.1
RELAY_2: J13.8, R19.2, R21.1
TEMP: J7.7 (GCLK0/GPIO4), J10.2, R13.1
WATER_BTN: C2.2, J7.11 (GPIO17), R11.1, SW2.2
WATER_CLOSURE: J3.2, J7.13 (GPIO27), R7.1
WATER_LED: J7.3 (SDA/GPIO2), R10.2
WATER_PUMP: J7.5 (SCL/GPIO3), R1.2, R2.1

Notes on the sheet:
HAT WATER TANK PANEL
THINGY COMMON
HAT NUTRI TANK PANEL
THINGY RELAY CONTROL
HAT RPI HEADER
HAT COMMON
STEP DOWN BOARD
HAT ATTINY85
THINGY HEATER CONTROL
JLCPCB PANELIZE CHEAT
THINGY LED CONTROL

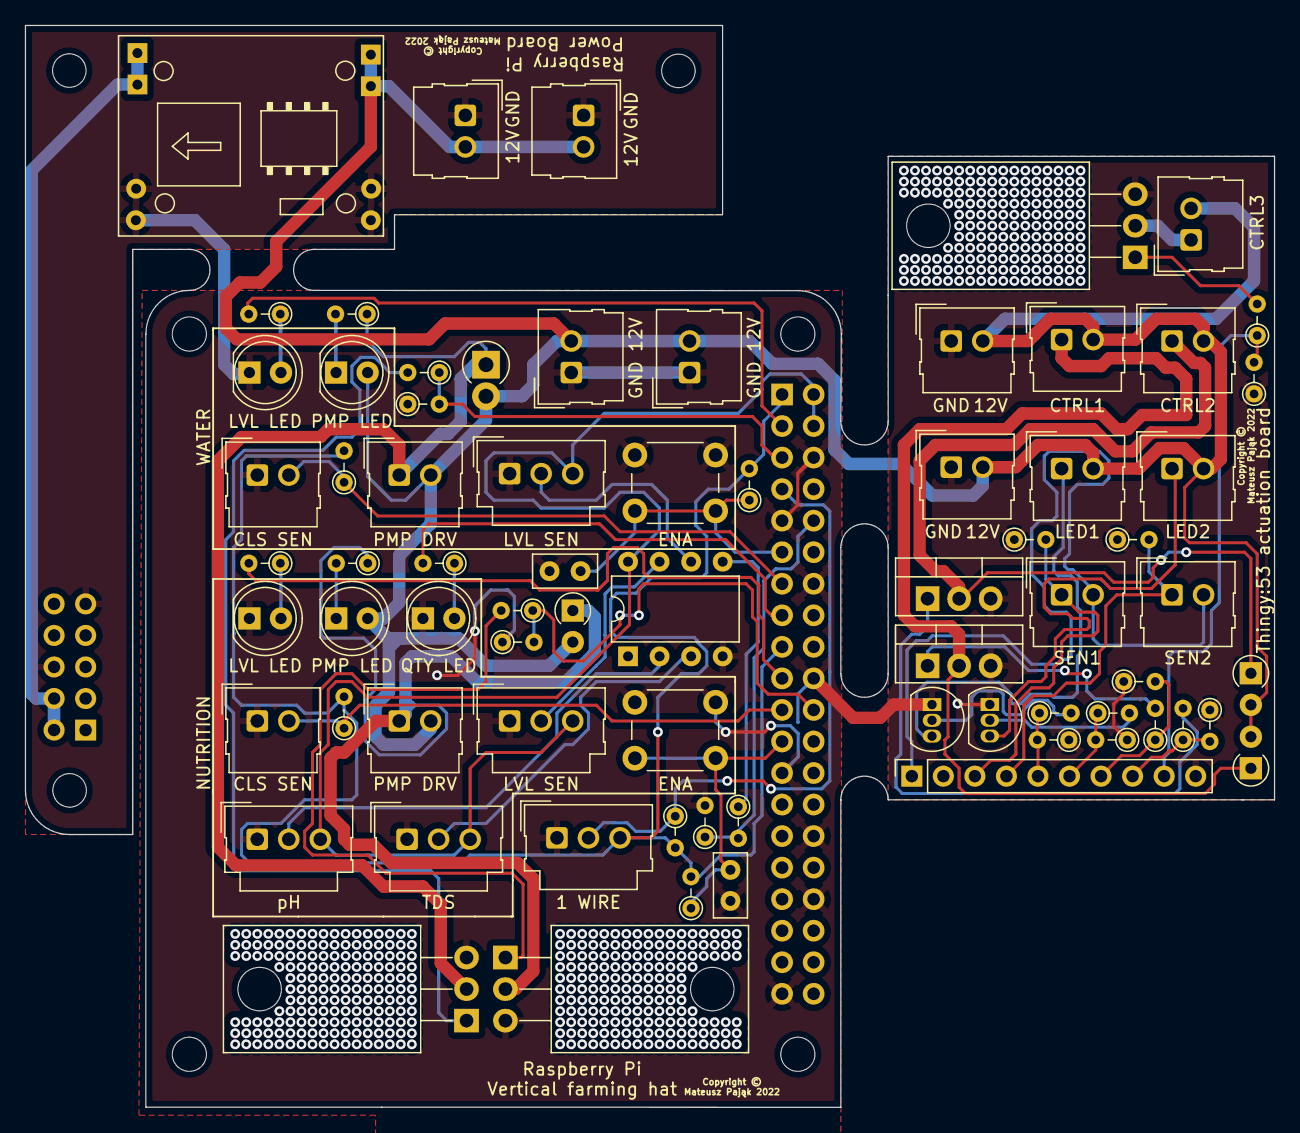
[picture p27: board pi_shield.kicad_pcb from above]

Board: 2 copper layers, 100.6 x 87.1 mm, 75 parts (1 on the bottom side), 48 nets.

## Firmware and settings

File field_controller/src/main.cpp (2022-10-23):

#include <zephyr.h>
#include <zephyr/settings/settings.h>
#include <zephyr/sys/reboot.h>
#include <zephyr/logging/log.h>
#include <zephyr/usb/usb_device.h>

#include "zigbee.hpp"
#include "sensors.hpp"
#include "controllers.hpp"
#include "classifier.hpp"
#include "config/hardware.hpp"
#include "config/software.hpp"

LOG_MODULE_REGISTER(main, MAIN_LOG_LEVEL);

namespace
{
	using DigOut = app::io::digital::Output;
	using AnOut = app::io::analog::PWM;
	using AnIn = app::io::analog::ADC;
	using ClosedController = app::io::controllers::ClosedController;
	using SensorResult = app::networking::zigbee::SensorResult;
	using EnvSensor = app::sensors::environmental::BME688;
	using Zigbee = app::networking::zigbee::ZigbeeInterface;
	using Classifier = app::inference::classifiers::Classifier;

	/**
	 * @brief Thread function to control growth lights.
	 * Control takes place only if ClosedControlStrategy == SELF.
	 */
	void lightCtrlThread();

	/**
	 * @brief Thread function to read sensors and publish them to Zigbee network.
	 */
	SensorResult sensorReadCallback();

	/**
	 * @brief Set control strategy for growth lights.
	 * Strat should be castable to ClosedControlStrategy.
	 */
	void lightStrategyCallback(uint16_t strat);

	/**
	 * @brief Set forced state of given ClosedController.
	 * This state will take effect only when ClosedControlStrategy is set to ZIGBEE.
	 *
	 * @tparam &controller
	 * @param val Value to set PWM output to (0 - 1023).
	 */
	template <ClosedController &controller>
	void lightControlCallback(uint16_t val);

	/**
	 * @brief Set state of given output.
	 *
	 * @tparam &actuator Output to use.
	 * @param val 0 - off, on otherwise.
	 */
	template <DigOut &actuator>
	void OutputControlCallback(uint16_t val);

	/**
	 * @brief Initialize all used hardware.
	 *
	 * @return True on success.
	 */
	bool initHardware();

	/**
	 * @brief Check whether all app's components are in good state.
	 */
	bool hardwareGood();

	/**
	 * @brief Signalize erroneous behavior to the user and reset the device.
	 */
	void handleCriticalError();
}

//****************
// Implementation.
//****************

namespace
{
	constexpr const gpio_dt_spec errPin = GPIO_DT_SPEC_GET(ERROR_PIN, gpios);
	constexpr const gpio_dt_spec blinkPin = GPIO_DT_SPEC_GET(BLINK_PIN, gpios);
	constexpr const gpio_dt_spec waterPin = GPIO_DT_SPEC_GET(WATER_PIN, gpios);
	constexpr const gpio_dt_spec nutriPin = GPIO_DT_SPEC_GET(NUTRI_PIN, gpios);
	constexpr const gpio_dt_spec fanPin = GPIO_DT_SPEC_GET(FAN_PIN, gpios);

	EnvSensor envSensor(DEVICE_DT_GET(SENSOR_DEVICE));
	Classifier classifier;

	constexpr Zigbee &zigbee = Zigbee::getInterface();

	DigOut errLed = DigOut(errPin, "Error LED");
	DigOut blinkLed = DigOut(blinkPin, "Blink LED");

	DigOut relayWater = DigOut(waterPin, "Water Valve");
	DigOut relayNutri = DigOut(nutriPin, "Nutri Valve");
	DigOut fan = DigOut(fanPin, "Air Fan");

	constexpr const device *ledDevice = DEVICE_DT_GET(LED_PWM);
	constexpr const device *ledSensorDevice = DEVICE_DT_GET(LED_ADC);

	ClosedController led1 = ClosedController(*ledDevice, LED1_CHANNEL,
											 *ledSensorDevice,
											 DT_IO_CHANNELS_INPUT_BY_IDX(DT_PATH(zephyr_user), LED1_ADC_CHANNEL));
	ClosedController led2 = ClosedController(*ledDevice, LED2_CHANNEL,
											 *ledSensorDevice,
											 DT_IO_CHANNELS_INPUT_BY_IDX(DT_PATH(zephyr_user), LED2_ADC_CHANNEL));

	K_THREAD_DEFINE(lightThreadId, LIGHT_CTRL_THREAD_STACK_SIZE,
					lightCtrlThread, NULL, NULL, NULL,
					1, 0, 10000);
}

#ifdef DATASET_COLLECTOR
int main()
{
	if (usb_enable(NULL))
	{
		LOG_ERR("Failed to initialize USB");
		handleCriticalError();
	}

	LOG_INF("Application core starting");

	k_sleep(K_SECONDS(5));

	if (!initHardware())
	{
		LOG_ERR("Hardware initialization failed");
		handleCriticalError();
	}

	while (hardwareGood())
	{
		k_sleep(K_MSEC(100));
		SensorResult res = sensorReadCallback();
		printk("%.3f, %.3f, %.3f, %.3f\n", res.temperature, res.pressure, res.humidity, res.gasResistance / 10000.0);
	}

	handleCriticalError();

	return 0;
}
#else
int main()
{
	if (usb_enable(NULL))
	{
		LOG_ERR("Failed to initialize USB");
		handleCriticalError();
	}

	LOG_INF("Application core starting");

	k_sleep(K_SECONDS(5));

	using ZigbeeCallbackType = app::networking::zigbee::CallbackType::Values;
	zigbee.registerCallback(ZigbeeCallbackType::FAN, OutputControlCallback<fan>);
	zigbee.registerCallback(ZigbeeCallbackType::RELAY_WATER, OutputControlCallback<relayWater>);
	zigbee.registerCallback(ZigbeeCallbackType::RELAY_NUTRI, OutputControlCallback<relayNutri>);
	zigbee.registerCallback(ZigbeeCallbackType::LED_SIDE_1, lightControlCallback<led1>);
	zigbee.registerCallback(ZigbeeCallbackType::LED_SIDE_2, lightControlCallback<led2>);
	zigbee.registerCallback(ZigbeeCallbackType::LED_STRATEGY, lightStrategyCallback);
	zigbee.registerSensorCallback(sensorReadCallback);

	if (settings_subsys_init())
	{
		LOG_ERR("Settings initialization failed");
		handleCriticalError();
	}

	if (!initHardware())
	{
		LOG_ERR("Hardware initialization failed");
		handleCriticalError();
	}

	classifier.init();

	if (settings_load())
	{
		LOG_ERR("Settings load failed");
		handleCriticalError();
	}

	zigbee.doWorkDetached();

	while (hardwareGood())
	{
		k_sleep(K_SECONDS(5));
		LOG_DBG("Blinking");

		if (!zigbee.isIdentifying())
		{
			blinkLed.setState(1);
			k_sleep(K_MSEC(100));
			blinkLed.setState(0);
		}
	}
	handleCriticalError();
	return 0;
}
#endif

namespace
{
	void lightCtrlThread()
	{
		while (hardwareGood())
		{
			if (led1.getControlStrategy() == ClosedController::ControlStrategy::SELF)
			{
				LOG_DBG("Updating growth light intensity");
				led1.update();
				led2.update();
				LOG_DBG("Growth light control updated");
			}
			else
			{
				LOG_DBG("Growth lights are in ZIGBEE state - skipping update ");
			}
			k_sleep(K_MSEC(100));
		}
		LOG_ERR("Hardware failure detected - stopping light control thread");
	}

	SensorResult sensorReadCallback()
	{
		SensorResult res;

		LOG_INF("Performing sensor read");
		if (!envSensor.read())
		{
			LOG_ERR("Failed to read environmental sensor");
			res.ok = false;
			return res;
		}

		res.temperature = envSensor.getTemperature();
		res.humidity = envSensor.getHumidity();
		res.pressure = envSensor.getPressure();
		res.gasResistance = envSensor.getGasResistance();
		res.classification = static_cast<uint8_t>(classifier.readNetwork(res.temperature, res.pressure, res.humidity, res.gasResistance));

		if (hardwareGood())
		{
			res.ok = true;
			LOG_INF("Sensor read done");
		}
		else
		{
			LOG_ERR("Hardware failure detected - skipping sensor read");
			res.ok = false;
		}

		return res;
	}

	void lightStrategyCallback(uint16_t strat)
	{
		if (strat > 1)
		{
			LOG_WRN("Invalid control strategy - ignoring");
			return;
		}
		bool stratBool = strat;
		auto stratEnum = static_cast<ClosedController::ControlStrategy>(stratBool);

		led1.setControlStrategy(stratEnum);
		led2.setControlStrategy(stratEnum);

		if (stratEnum == ClosedController::ControlStrategy::SELF)
		{
			LOG_INF("Growth light control set to SELF");
		}
		else
		{
			LOG_INF("Growth light control set to ZIGBEE");
		}
	}

	template <ClosedController &controller>
	void lightControlCallback(uint16_t val)
	{
		if (val > 1023)
		{
			LOG_WRN("Value %d passed to %s is out of allowed bounds [0 - 1023] - ignoring", val, "TODO");
			return;
		}
		LOG_INF("Setpoint for %s set to %d", "TODO", val);
		controller.setState(val);
	}

	template <DigOut &actuator>
	void OutputControlCallback(uint16_t val)
	{
		LOG_INF("Value of %s set to %d", actuator.getLabel(), val);
		actuator.setState(val);
	}

	bool initHardware()
	{
		LOG_INF("Initializing hardware");
		if (!errLed.init())
		{
			LOG_ERR("Ironic - error LED init failed");
			return false;
		}
		if (!blinkLed.init())
		{
			LOG_ERR("Blink LED init failed");
			return false;
		}
		if (!led1.init())
		{
			LOG_ERR("Growth LED 1 init failed");
			return false;
		}
		if (!led2.init())
		{
			LOG_ERR("Growth LED 2 init failed");
			return false;
		}
		if (!relayWater.init())
		{
			LOG_ERR("Water relay init failed");
			return false;
		}
		if (!relayNutri.init())
		{
			LOG_ERR("Nutri relay init failed");
			return false;
		}
		if (!fan.init())
		{
			LOG_ERR("Fan init failed");
			return false;
		}
		if (!envSensor.init())
		{
			LOG_ERR("Environmental sensor init failed");
			return false;
		}
		if (!zigbee.init())
		{
			LOG_ERR("Zigbee init failed");
			return false;
		}
		LOG_INF("Hardware initialized properly");
		return true;
	}

	bool hardwareGood()
	{
		LOG_DBG("Checking status of application's hardware");
		if (!errLed.ok())
		{
			LOG_ERR("Ironic - error LED failed");
			return false;
		}
		if (!blinkLed.ok())
		{
			LOG_ERR("Blink LED failed");
			return false;
		}
		if (!led1.ok())
		{
			LOG_ERR("Growth LED 1 failed");
			return false;
		}
		if (!led2.ok())
		{
			LOG_ERR("Growth LED 2 failed");
			return false;
		}
		if (!relayWater.ok())
		{
			LOG_ERR("Water relay failed");
			return false;
		}
		if (!relayNutri.ok())
		{
			LOG_ERR("Nutri relay failed");
			return false;
		}
		if (!fan.ok())
		{
			LOG_ERR("Fan failed");
			return false;
		}
		if (!envSensor.ok())
		{
			LOG_ERR("Environmental sensor failed");
			return false;
		}
		if (!zigbee.ok())
		{
			LOG_ERR("Zigbee failed");
			return false;
		}
		LOG_DBG("Hardware good");
		return true;
	}

	void handleCriticalError()
	{
		if (blinkLed.ok())
		{
			blinkLed.setState(0);
		}
		if (zigbee.ok())
		{
			zigbee.cleanup();
		}
		if (errLed.ok())
		{
			for (uint8_t i = 0; i < 10; i++)
			{
				k_sleep(K_MSEC(200));
				errLed.setState(1);
				k_sleep(K_MSEC(200));
				errLed.setState(0);
			}
		}
		LOG_ERR("System error encountered, performing hard reboot");

		k_sleep(K_SECONDS(1));
		sys_reboot(SYS_REBOOT_WARM);
	}
}

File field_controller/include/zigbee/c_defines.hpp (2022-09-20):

#pragma once

#define BASIC_APP_VER 1
#define BASIC_ZB_STACK_VER 10
#define BASIC_HW_VER 1
#define BASIC_MANUF_NAME "Nordic"
#define BASIC_MODEL_ID "FC_v0.1"
#define BASIC_DATE_CODE "20220914"
#define BASIC_POWER_SOURCE ZB_ZCL_BASIC_POWER_SOURCE_DC_SOURCE
#define BASIC_LOCATION "Field"
#define BASIC_ENV ZB_ZCL_BASIC_ENV_UNSPECIFIED

#define ZIGBEE_NETWORK_STATE_LED DK_LED2
#define IDENTIFY_LED DK_LED3
#define IDENTIFY_MODE_BUTTON DK_BTN2_MSK
#define FACTORY_RESET_BUTTON IDENTIFY_MODE_BUTTON

#define ZB_FAN_ENDPOINT 10
#define ZB_LED1_ENDPOINT 11
#define ZB_LED2_ENDPOINT 12
#define ZB_STRATEGY_ENDPOINT 13
#define ZB_WATER_ENDPOINT 14
#define ZB_NUTRI_ENDPOINT 15

#define ZB_DEV_ID 0x2137
#define ZB_DEV_VER 1

#define ZB_IN_CLUSTER_NUM 10
#define ZB_OUT_CLUSTER_NUM 0 // TODO: Change
//#define ZB_TOTAL_CLUSTER_NUM (ZB_IN_CLUSTER_NUM + ZB_OUT_CLUSTER_NUM)

// TODO: Change???
#define ZB_REPORT_ATTR_COUNT (ZB_ZCL_ON_OFF_REPORT_ATTR_COUNT + ZB_ZCL_LEVEL_CONTROL_REPORT_ATTR_COUNT)

// TODO: Change???
#define ZB_CVC_ATTR_COUNT 1

/**
 * @brief Declare cluster list for on / off device
 * @param cluster_list_name - cluster list variable name
 * @param basic_attr_list - attribute list for Basic cluster
 * @param identify_attr_list - attribute list for Identify cluster
 * @param groups_attr_list - attribute list for Groups cluster
 * @param scenes_attr_list - attribute list for Scenes cluster
 * @param on_off_attr_list - attribute list for On/Off cluster
 */
#define ZB_DECLARE_ON_OFF_CLUSTER_LIST(                               \
    cluster_list_name,                                                \
    basic_attr_list,                                                  \
    identify_attr_list,                                               \
    groups_attr_list,                                                 \
    scenes_attr_list,                                                 \
    on_off_attr_list)                                                 \
    zb_zcl_cluster_desc_t cluster_list_name[] =                       \
        {                                                             \
            ZB_ZCL_CLUSTER_DESC(                                      \
                ZB_ZCL_CLUSTER_ID_IDENTIFY,                           \
                ZB_ZCL_ARRAY_SIZE(identify_attr_list, zb_zcl_attr_t), \
                (identify_attr_list),                                 \
                ZB_ZCL_CLUSTER_SERVER_ROLE,                           \
                ZB_ZCL_MANUF_CODE_INVALID),                           \
            ZB_ZCL_CLUSTER_DESC(                                      \
                ZB_ZCL_CLUSTER_ID_BASIC,                              \
                ZB_ZCL_ARRAY_SIZE(basic_attr_list, zb_zcl_attr_t),    \
                (basic_attr_list),                                    \
                ZB_ZCL_CLUSTER_SERVER_ROLE,                           \
                ZB_ZCL_MANUF_CODE_INVALID),                           \
            ZB_ZCL_CLUSTER_DESC(                                      \
                ZB_ZCL_CLUSTER_ID_SCENES,                             \
                ZB_ZCL_ARRAY_SIZE(scenes_attr_list, zb_zcl_attr_t),   \
                (scenes_attr_list),                                   \
                ZB_ZCL_CLUSTER_SERVER_ROLE,                           \
                ZB_ZCL_MANUF_CODE_INVALID),                           \
            ZB_ZCL_CLUSTER_DESC(                                      \
                ZB_ZCL_CLUSTER_ID_GROUPS,                             \
                ZB_ZCL_ARRAY_SIZE(groups_attr_list, zb_zcl_attr_t),   \
                (groups_attr_list),                                   \
                ZB_ZCL_CLUSTER_SERVER_ROLE,                           \
                ZB_ZCL_MANUF_CODE_INVALID),                           \
            ZB_ZCL_CLUSTER_DESC(                                      \
                ZB_ZCL_CLUSTER_ID_ON_OFF,                             \
                ZB_ZCL_ARRAY_SIZE(on_off_attr_list, zb_zcl_attr_t),   \
                (on_off_attr_list),                                   \
                ZB_ZCL_CLUSTER_SERVER_ROLE,                           \
                ZB_ZCL_MANUF_CODE_INVALID)}
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

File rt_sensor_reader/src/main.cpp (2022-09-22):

#ifdef BLINK_TEST
#include "timer.hpp"
#else
#include <util/delay.h>
#include "transmitter.hpp"
#include "level_sensor.hpp"
#include "ph_sensor.hpp"
#include "tds_sensor.hpp"
#include "hw_definitions.hpp"
#endif

#ifndef BLINK_TEST
int main()
{
  _delay_ms(30000);
  transmitter_setup();
  usensor_commonSetup();
  phsensor_setup();
  tdssensor_setup();

  while (true)
  {
    transmitter_sendMeasurement(u0Prefix, usensor_read(u0));
    transmitter_sendMeasurement(u1Prefix, usensor_read(u1));
    transmitter_sendMeasurement(phPrefix, phsensor_read());
    transmitter_sendMeasurement(ecPrefix, tdssensor_read());
    _delay_ms(10);
  }
}
#else
int main()
{
  timer_setup();
  DDRB |= (1 << DDB0);

  while (true)
  {
    PORTB |= (1 << PB0);
    timer_reset();
    while (timer_read() < 1000000L)
      ;
    PORTB &= ~(1 << PB0);
    timer_reset();
    while (timer_read() < 1000000L)
      ;
  }
}
#endif

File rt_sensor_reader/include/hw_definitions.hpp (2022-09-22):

#pragma once
#include <stdint.h>
#include <avr/io.h>

constexpr uint8_t serial = PB0;

constexpr char u0Prefix[] = "u0";
constexpr uint8_t u0 = PB1;

constexpr char u1Prefix[] = "u1";
constexpr uint8_t u1 = PB2;

constexpr char phPrefix[] = "ph";
constexpr uint8_t ph = PB3;

constexpr char ecPrefix[] = "tds";
constexpr uint8_t ec = PB4;

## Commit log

2022-08-26 Add pi shield design files
    [pi_shield.kicad_pcb, pi_shield.kicad_sch]
2022-08-29 Finish PCBs
    [pi_shield-B_Cu.gbl, pi_shield-B_Mask.gbs, pi_shield-B_Paste.gbp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]
2022-09-20 Modify field_controller, stamp rt_sensor_reader before remove Arduino UNO debug code
2022-09-22 Tune tds and ph sensors
2022-09-22 Add platformio.ini build flags for tds and ec sensors
2022-09-26 Replace EC with TDS in uc_bridge
    [uc_bridge.py]
2022-09-26 Fix naming in submodules/common
    [common.py, level_observer.py, quality_observer.py]
2022-09-26 Add temperature observer
2022-09-27 Add temperature measurement
2022-09-28 Make Field Controller upload to the device
2022-09-30 Resolve bug with field controller not starting w/ zigbee stack enabled
    [gpio.cpp, hardware.hpp, main.cpp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]
2022-10-10 Finish frontend, add state publisher to pump driver
2022-10-10 Add garden meta package, fix some bugs
    [params.yaml, quality_observer.py, temperature_observer.py]
2022-10-24 Add STL files
    [funnel.stl, heater_bottom_1.stl, heater_bottom_2.stl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]
2022-10-24 Bug fixes and param fixes
    [params.yaml, temperature_observer.py]

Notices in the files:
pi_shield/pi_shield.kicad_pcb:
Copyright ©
